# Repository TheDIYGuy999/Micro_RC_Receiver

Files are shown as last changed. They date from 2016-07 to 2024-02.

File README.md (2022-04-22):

# This is an ATMEL Mega328P / NRF24L01+ based 2.4GHz radio receiver
## Features:
- Compatible with this transmitter: https://github.com/TheDIYGuy999/RC_Transmitter
- Programmable with Arduino IDE
- 4 RC servo connectors
- SBUS output
- Outputs for Headlights, indicators, taillights with brake lights
- Additional switching output
- Support for self balancing robot or car with stability control (using an MPU-6050 sensor)
- Integrated TB6612FNG dual dc motor driver
- Serial header (with SBUS support)
- I2C header (for example for the supported MPU-6050)
- ICSP header for programming with Arduino IDE (use "TheDIYGuy999 328P" board definition and set brownout voltage to 1.8V)
- NRF24L01+ SMD module integrated
- very small size
- Up to 20 vehicle addresses selectable, allows to use the same remote controller for 10 vehicles
- Eagle & Gerber files are also provided, if you want to build your own receiver!

See: https://www.youtube.com/playlist?list=PLGO5EJJClJBCjIvu8frS7LrEU3H2Yz_so

New in V 1.3:
- Vehicle configuration is now stored in "vehicleConfig.h", so the main code always stays the same.
- Crude frequency hopping, if bad receiving quality is detected (needs to be improved).

New in V 1.4:
- 10 vehicle addresses instead of 5
- More vehicle configuration options
- The "BACK" button on the transmitter can now be used (if the menu screen is not displayed on the OLED) as a momentary button, for example for a horn on the vehicle. It is sent as "data.momentary1"
- SimpleTimer library replaced with my own code, which uses significantly less memory

New in V 1.5:
- Added steering mixer for semi caterpillar and caterpillar vehicles such as tanks, diggers etc.
- Channel 3 is throttle, channel 1 is steering
- More vehicle configuration options in vehicleVonfig.h
- The left caterpillar is motor 2, the right is motor 1
- Steering servo 1 can be used in parallel (for semi caterpillar vehicles or vehicles with electronic differential)

New in V 1.6:
- Added indicator lights - wired to A4 (SDA) / A5 (SCL) ports
- enabled and disabled left / right by channel 4 left / right
- disabled by turning back the steering wheel (channel 1) - just like a real car
- hazard lights (all indicators flashing), if no connection to the transmitter

New in V 1.61:
- Battery cutoff bug fixed

New in V 1.7 (Support for board revision 1.3):
- **** TB6612FNG library update to V1.1 is required! ****
- motor driver pinout has changed in board V1.3. So we are now able to adjust the PWM frequency of motor2. This allows smooth motor operation without the typical PWM whining.
- vehicleConfig.h changed: "boardVersion" and "HP" variables added. They allow to stay compatible with older board versions. Just select the correct configuration.
- The new "HP" (High Power) board version has only one motor driver channel, because both TB6612FNG channels are wired in parallel. It's able to supply 2.4A (average) / 6.4A (peak) so we can use bigger motors. This is useful for models, which use a steering servo and don't need a second motor channel.'
- automatic radio re-initialisation after signal timeout

New in V 1.71
- Battery monitoring and cutoff triggering improved. Under load, 0.3V are now added to the battery voltage to compensate the voltage drop. This allows to set the cutoff voltage to 3.6V, even with bigger loads.
- Vehicle #7 added.

New in V 1.8
- New "engineSound" variable in "vehicleconfig.h". True means, that the servo 3 pulse signal can be switched on and off, using the  channel 2 joystick. This switches the engine sound on my "Rc Engine Sound" unit on and off.

New in V 1.9
- New vehicle specific configuration section in vehicleConfig.h. The configuration is now done entirely during compilation time.

New in V 2.0
- vehicle Config.h: New vehicleType 3 (forklift) added. Motor 2 is used as lifting motor in this case. A servo is required as steering motor.
- Beacon lights can be wired to servo channel 4. Select "beacons = true" in this case. The beacons are flashing during vehicle movement and are switching off, after the vehicle did not move for 10s.

New in V 2.1
- Sounds for a STAR WARS R2-D2 robot can now be generated on servo channel 3
- "toneOut" variable added to vehicleConfig.h. True means, that servo 3 channel is generating sounds instead of a servo signal.
- Do not enable "toneOut" and "engineSound" at the same time.
- Note: the Arduino tone() function is blocking. So don't play sounds while driving ;-)

New in V 2.2
- **** TB6612FNG library update to V1.2 is required! **** https://github.com/TheDIYGuy999/TB6612FNG
- **** The PID library is required! **** https://github.com/br3ttb/Arduino-PID-Library/
- Support for self balancing (inverted pendulum, segway) vehicles. See: https://www.youtube.com/watch?v=zse9-l2Yo3Y)
- A MPU-6050 accelerometer & gyro module is used for the balancing data communication via SDA & SCL
- Note, that the receiver will not work, if your vehicleType is 4 (balancing) and no MPU-6050 is connected!
- Do not enable "balancing" and "indicators" at the same time.

New in V 2.21
- Gyro drift calibration bug fixed
- Changed the balancing controller refresh rate to 125Hz to reduce jitter on a 8MHz MCU. Reason: one program loop takes 4 - 7ms, so we can't use a time base of 4ms (=250Hz).

New in V 2.3
- MRSC (Micro RC Stability Control) added. This functionality is similar to the Traxxas TSM or ESC. See: https://www.youtube.com/watch?v=IPve7QpdLBc&t=5s
- The steering servo angle is compensated in accordance with the speed, the requested steering angle and the measured yaw rate, which is coming from the MPU-6050
- Basically the mrsc() function was added. The required yaw rate is already calculated in the balancing.h, which is already existing for self balancing robots
- If you want to use this functionality, you have to set the vehicleType to 5 in the vehicleConfig.h. Please note, that the receiver will not work, if no MPU-6050 is connected and the vehicleType is set to 4 or 5!

New in V 2.31
 - MRSC gain factor now depending on the potentiometer 1 value on the transmitter
 - Allows to fine adjust the MRSC during driving, depending on the requirements of the street surface
 - Note, that you need to connect a potentiometer to the analog input A6 of your transmitter!
 
 New in V 2.32
 - Flickering headlights bug in vehicleType 5 fixed
 - The accelerometer vectors are not processed anymore in vehicleType 5. This is only required for the self balancing robot (vehicleType 4)
 
 New in V 2.4
 - The I2C bus is scanned for an MPU-6050 sensor during the setup() sequence. The vehicleType is automatically changed to 0 (car without MRSC), if no sensor is detected.
 - This means, that a car with vehicleType 5 (MRSC Stability Control) can now also be used without an MPU-6050 plugged in.
 - Note, that the self balancing mode (vehicleType 4) always requires an MPU-6050. Otherwise the receiver will not start.
 
 New in V 2.41
 - The "indicators" variable is now locked and can't be enabled, if the SDA and SCL pins are in use for the MPU-6050 sensor. This is the case in vehicleMode 4 and 5.
 
 New in V 2.5
 - The MRSC stability control is now also working for cars without a steering servo
 - Code was added to control a DC steering motor (as found in cheap RC cars) in accordance with the MPU-6050 yaw rate
 - This is for example very useful for Coke Can Cars. See: https://www.youtube.com/watch?v=jr5yYBal3vk
 
 New in V 2.6
 - The MRSC stability control can now be used with transmitters without gain adjustment potentiometer
 - The following optional parameters in the vehicleConfig.h allow to use a fixed gain: MRSC_FIXED, mrscGain
 - Allows to add an MPU-6050 gyro to every vehicle. So we always have a closed loop steering control, even without a proper servo with potentiometer feedback
 - On the "Non-High-Power" receiver model, 0.3V battery voltage are not added anymore during driving. This is not useful, if there is not much current draw.
 
 New in V 2.7
 - The MRSC stability control gain adjustment knob can now be linked to servo CH4, if "potentiometer1" is set to "true" in vehicleConfig.h
 - This is useful, if an external MRSC stability control unit for 3 pin servos is used. See: https://github.com/TheDIYGuy999/MRSC_Adapter_3Pin_Servo
 - Servo CH4 is wired to pin 5 in this case. This allows to adjust the MRSC gain on the transmitter, just as with the internal MRSC stability control
 
 New in V 2.8
 - Added support for differential thrust controlled airplanes
 - Tested with a Piper J3 CUB from Banggood
 
 New in V 2.9
 - Added TWO_SPEED_GEARBOX option for mechanical two speed gearboxes, shifted by a servo, connected to CH2, controlled by "Mode 1" button
 - Example see vehicle CONFIG_WPL_B-36
 - See video: https://www.youtube.com/watch?v=EaOJE_GU5pk&t=1s
 
 New in V 3.0
 - Added TRACTOR_TRAILER_UNLOCK option. Used to operate the tractor trailer unlocking servo
 - Press the "Back / Pulse" button to unlock your trailer
 - See vehicle "CONFIG_JJRC_Q60" for example
 - Parts for 3D printing: https://www.thingiverse.com/thing:3399449
 
 New in V 3.1
 - Added THRE_SPEED_GEARBOX option for mechanical three speed gearboxes, shifted by a servo, connected to CH2, controlled by a 3 position switch, connected to CH2 Joystick input of the transmitter. A 10k resistor is reqired between GND and the input pin as well as between the input pin and VCC
 - Three individual servo positions can be programmed: lim2L, lim2C, lim2R
 - Example see vehicle CONFIG_HG_P407
 
 New in V 3.2
 - Added the "TXO_toggle1" variable: allows to toggle the TXO pin, using the "Back / Impulse" button on the transmitter
 - Useful for example for additional lights
 - Don't activate it in combination with "TXO_momentary1". Serial is not usable, if one of these booleans is set to true
 
 New in V 3.3
 - Added experimental support for serial communication with my "Arduino RC engine sound generator for ESP32": https://github.com/TheDIYGuy999/Rc_Engine_Sound_ESP32
 - Uncomment "#define SERIAL_COMMUNICATION" in Adjustments.h of the sound generator
 - Connect pin 36 "VP"of the sound generator  to pin "TXO" of the receiver (disable "TXO_momentary1", "TXO_toggle1" & "headLights" in vehicleConfig.h)
 
 New in V 3.31
 - "headlLights" must be inactive as well in order to use serial communication!
 
 New in V 3.32
 - "data.pot1" properly initialized (cauesd an issue on the ESP32 engine sound generator)
 
 New in V 3.4
 - SBUS support added (variable "SBUS_SERIAL" in vehicleConfiguration.h
 - Channel order and comments see sendSbusCommands()
 - You need to install my SBUS library: https://github.com/TheDIYGuy999/SBUS
 - Connect your servos or what ever to pin "TXO"  (disable "TXO_momentary1", "TXO_toggle1" & "headLights" in vehicleConfig.h)
 
 New in V 3.5
 - mode1, mode2 and momentary1 properly initialised before SBUS is enabled
 
 New in V 3.6
 - "vehicleType" 1 or 2 (tracked or half tracked mode steering mixer) is now working as well, if two ESC are connected to servo pins 2 and 3. In the past, it was only usable with the internal TB6612 dual DC motor driver.
 - Also works in combination with my ESP32 Engine Sound & Light Controller (SBUS & PWM Mode)
 
 New in V 3.7
 - Steering center position separately adjustable, using "#define STEERING_3_POINT_CAL" and "lim1C". This is useful for badly designed steering linkage geometries. Example see vehicle configuration "CONFIG_WPL_B_36_MODE1"
 
 New in V 3.8:
 - 20 vehicle addresses instead of 10
 - Less RAM usage
 - 2 speed transmission not shifting while standing still. This will protect the shifting servo.

New in V 3.81:
 - Libraries comments added
 
 New in V 3.9:
 - New "#define VEHICLE_TYPE_3_WITH_ESC" option for vehicle type 3. Allows to use both TB6612 FNG motor driver channels for other stuff
 - Used in "CONFIG_MECCANO_DUMPER"

## Usage

See pictures

Newest version v1.5:
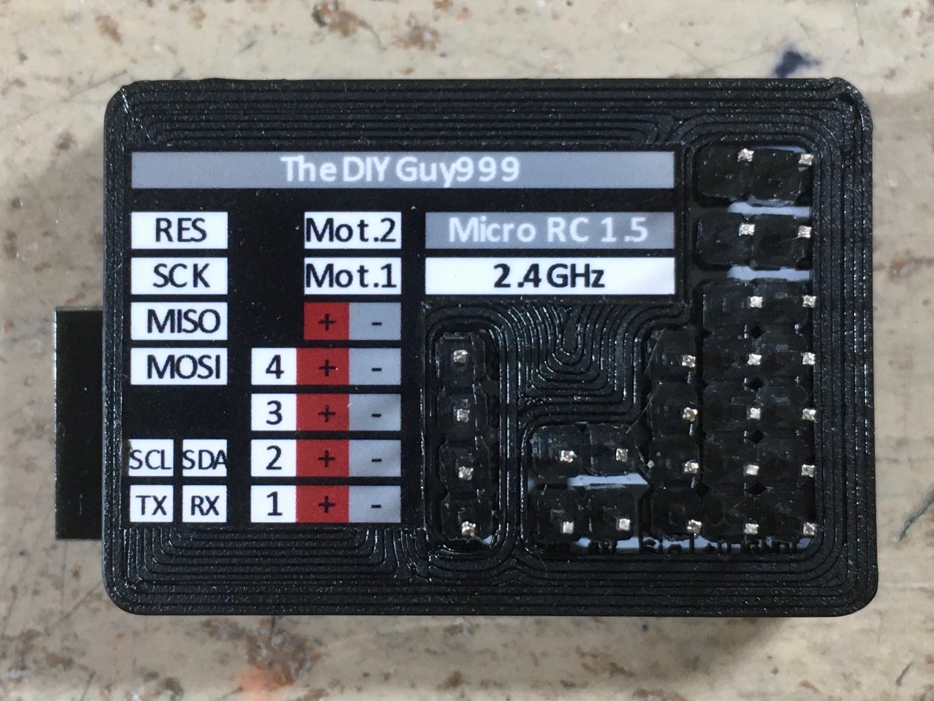
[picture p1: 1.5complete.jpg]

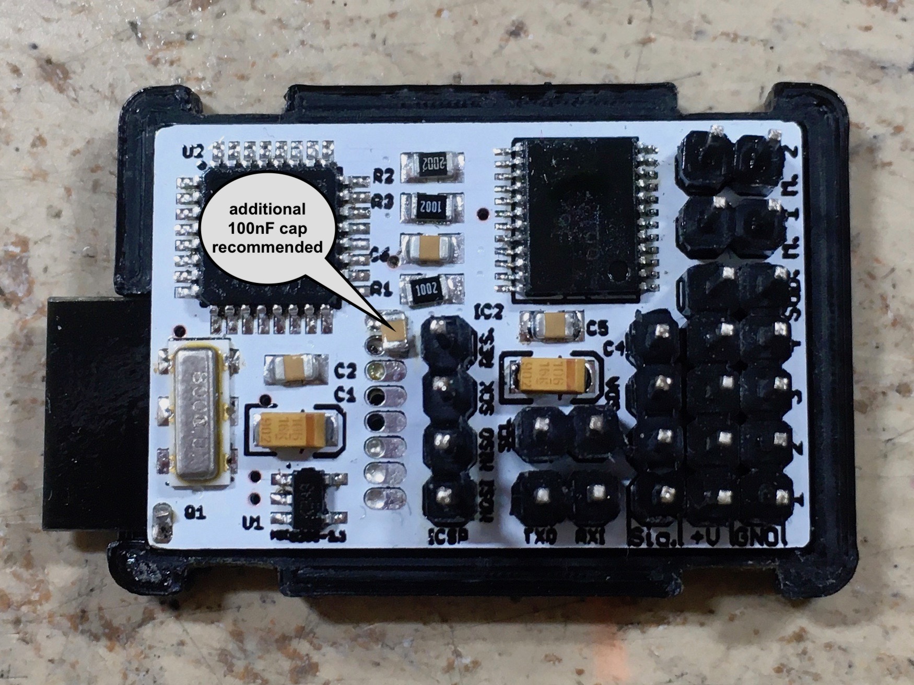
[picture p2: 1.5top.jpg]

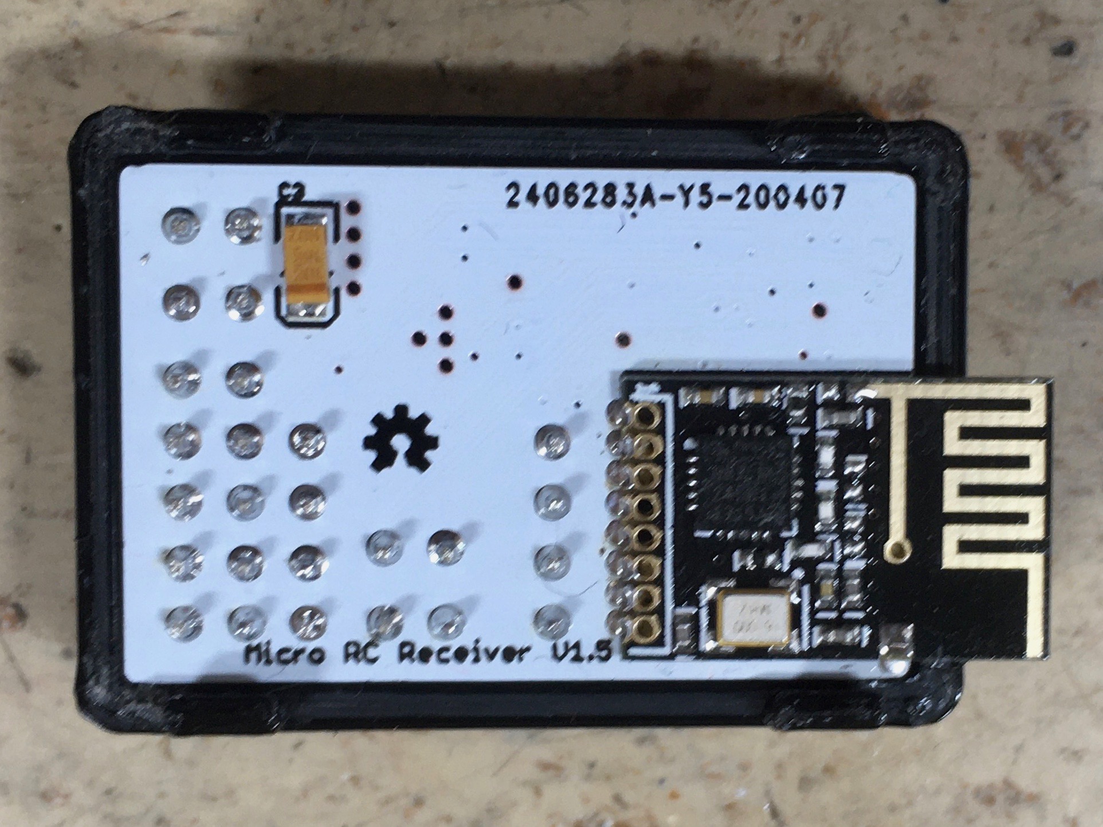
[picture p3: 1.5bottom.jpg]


First prototype:
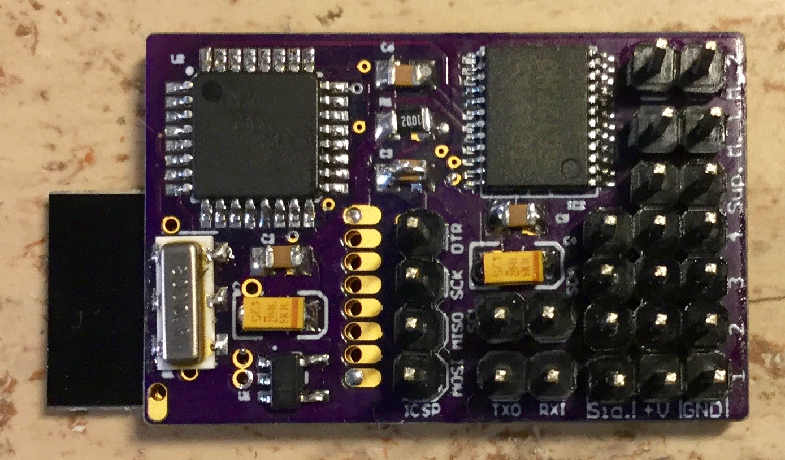
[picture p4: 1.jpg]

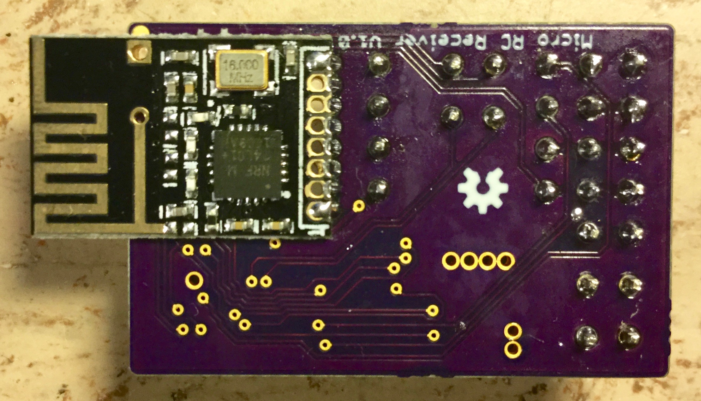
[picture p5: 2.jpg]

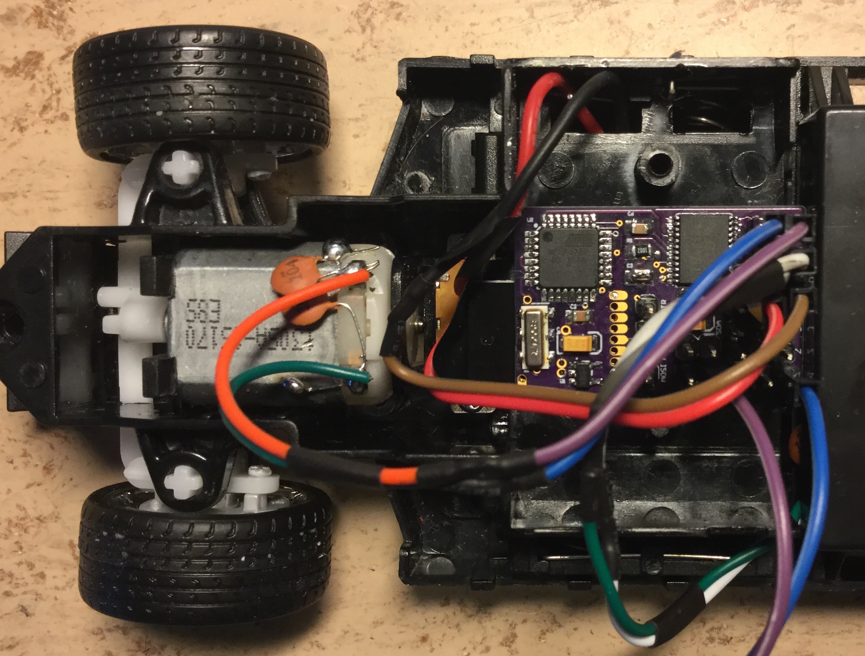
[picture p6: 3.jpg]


Receiver PCB

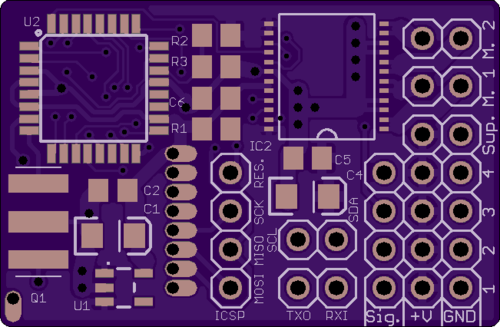
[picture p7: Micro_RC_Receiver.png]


MPU-6050 shield PCB

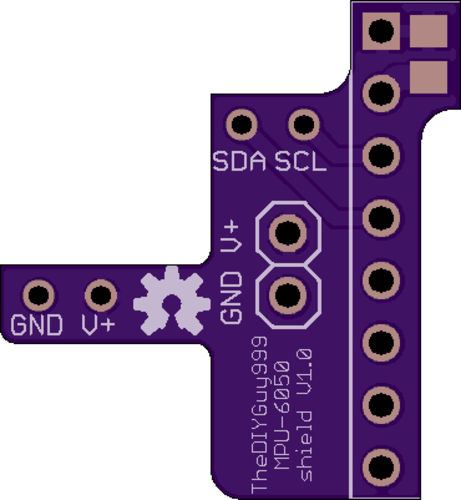
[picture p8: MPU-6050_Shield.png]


(c) 2016 - 2020 TheDIYGuy999

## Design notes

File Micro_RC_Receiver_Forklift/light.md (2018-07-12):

## light pins

|    light         |   pin  |
| ----------- ---- |   ---  |
|  tail light      | Servo2 |
|  head light      |  RXI   |
|  left indicator  |  SDA   |
|  right indicator |  SCL   |
|  beacon lights   | Servo4 |

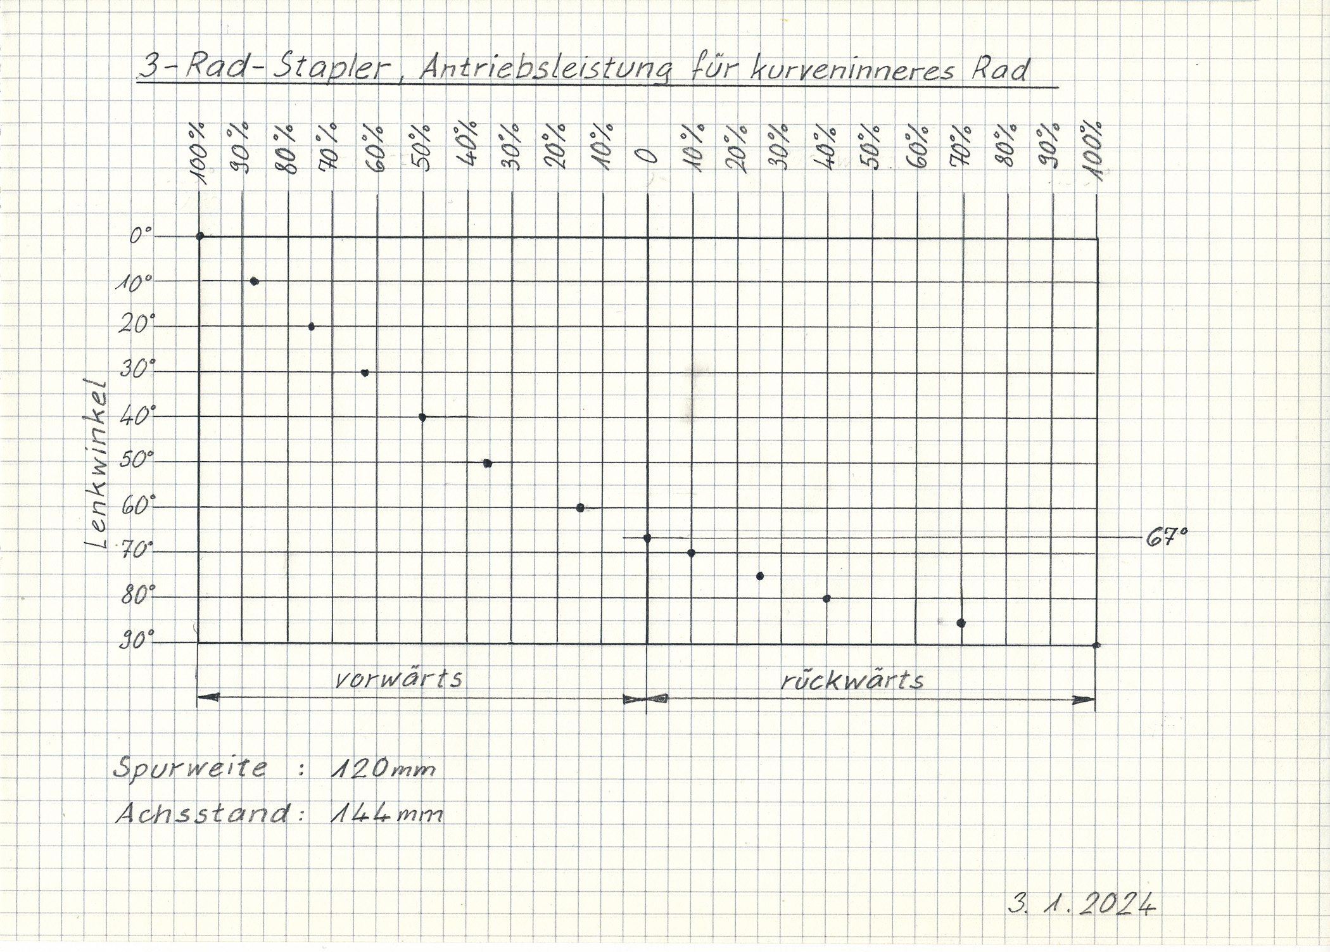
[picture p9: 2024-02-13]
Antriebaufteilung Stapler.jpg

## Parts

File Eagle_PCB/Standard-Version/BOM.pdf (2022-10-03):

## Micro RC Receiver Bill of Material

Qty. | Schematic | Package | Name | Value | Function | Manufacturor | Datasheet or Product Link
1 | U1 | SOT23-5 | MIC5205-3.3 | 3.3V | LDO 3.3V regulator | MICREL | http://ww1.microchip.com/downloads/en/DeviceDoc/mic5205.pdf
1 | U2 | TQFP32-08 | ATMEGA328P U-TH | | Microcontroller | MICROCHIP | http://www.atmel.com/images/Atmel-8271-8-bit-AVR-Microcontroller-ATmega48A-48PA-88A-88PA-168A-168PA-328-328P_datasheet_Complete.pdf
1 | IC1 | SMD PCB | NRF24L01+ | | Radio module (on a PCB) | NORDIC SEMI | https://www.sparkfun.com/datasheets/Components/SMD/nRF24L01Pluss_Preliminary_Product_Specification_v1_0.pdf
1 | IC2 | SSOP24 | TB6612FNG | | 2 Channel DC Motor Driver | TOSHIBA | https://www.sparkfun.com/datasheets/Robotics/TB6612FNG.pdf
1 | Q1 | SMT | CSTCC8M00G53-R0 | | 8MHz Resonator | MURATA | https://www.distrelec.ch/Web/Downloads/_t/ds/cstcc_g_eng_tds.pdf
3 | C1, C3, C4 | EIA3216 | T491A106K016AT | 16VDC, 10uF, Tantalum | Voltage smoothing | KEMET | https://www.distrelec.ch/Web/Downloads/_t/ds/KEM_T2005_T491_eng_tds.pdf
3 | C2, C5, C6 | 0805 | C0805C104K5RACTU | 50V, 100nF, Ceramic | Decoupling | KEMET | https://www.distrelec.ch/Web/Downloads/_t/ds/KEM_C1002_X7R_SMD_eng_tds.pdf
2 | R1, R3 | 0805 | CRCW080510K0FKEA | 10kOhm, +-1% | Reset Pullup, A7 Pulldown | Vishay | https://www.distrelec.ch/Web/Downloads/a_/en/flD-CRCW-e3_data_en.pdf
1 | R2 | 0805 | CRCW080520K0FKEA | 20kOhm, +-1% | A7 Pullup to VBAT | Vishay
10 | JP 1 - 10 | 0.1" | Pin Header | Male | Connectors | Generic

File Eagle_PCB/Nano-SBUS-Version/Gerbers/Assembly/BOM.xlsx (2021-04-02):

Comment | Designator | qty | Footprint | Additional Comment | 5sets Unite price | 5sets Total price | Note
ATmega328P-MU | U2 | 1 | MLF32-PAD | Arduino compatible | $3.675 | $18.375 | ATMEGA328P-MU
 | ~~IC1~~ |  | ~~NRF24L01_SMD_PAD~~ |  |  |  | DNP
 | ~~JP3, JP6~~ |  | ~~1X03_1.27~~ |  |  |  | DNP
 | ~~JP1~~ |  | ~~1X03_SMT~~ |  |  |  | DNP
 | ~~JP4~~ |  | ~~1X04_1.27~~ |  |  |  | DNP
 | ~~JP7~~ |  | ~~1X05_1.27~~ |  |  |  | DNP
 | ~~JP5~~ |  | ~~1X06_1.27~~ |  |  |  | DNP
100nF 50V | C2, C4 | 2 | C0603 |  | $0.052 | $0.525
10k | R1, R3 | 2 | R0603 |  | $0.052 | $0.525
10uF 16V Tantalum | C1 | 1 | EIA3216 |  | $0.210 | $1.050
20k | R2 | 1 | R0603 |  | $0.052 | $0.263
CSTNE8M00G550000R0 | Y2 | 1 | RESONATOR-SMD-3.2X1.3 | 8MhHz, Murata | $0.315 | $1.575
MIC5205-3.3 | U1 | 1 | SOT23-5 | 3.3V | $0.315 | $1.575 | MIC5205-3.3YM5-TR
 |  |  |  |  |  | $23.887 | Component price
 | Parts suppliers and tolerances are not important. Please ask back, if any of the SMD components can't be populated |  |  |  |  | $30.000 | assembly price
 |  |  |  |  |  | $15.000 | board price

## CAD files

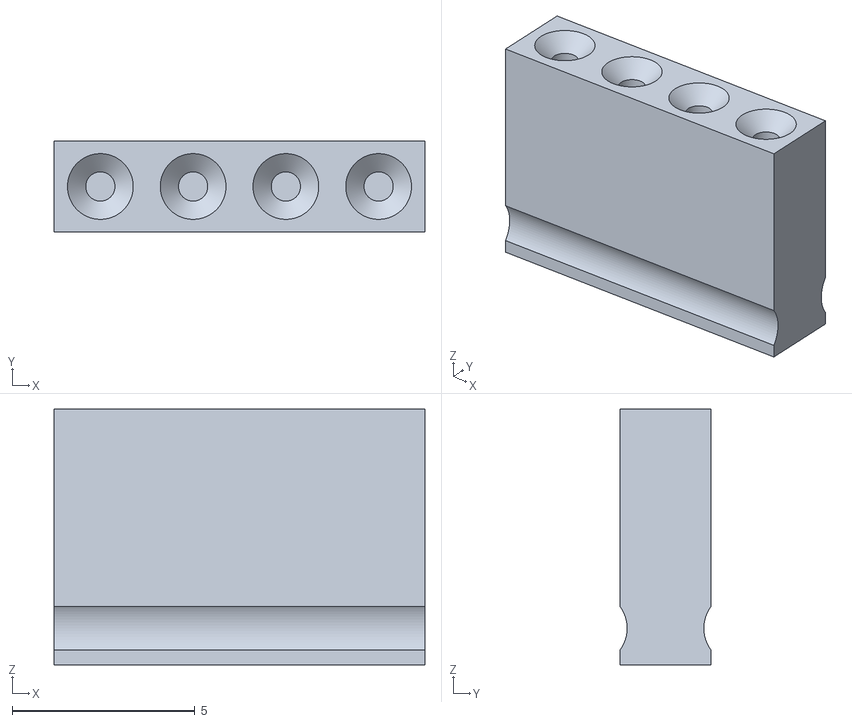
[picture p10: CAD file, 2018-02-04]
Housing/Pin Header Cover 4x.stl
10.2 x 2.50 x 7.00

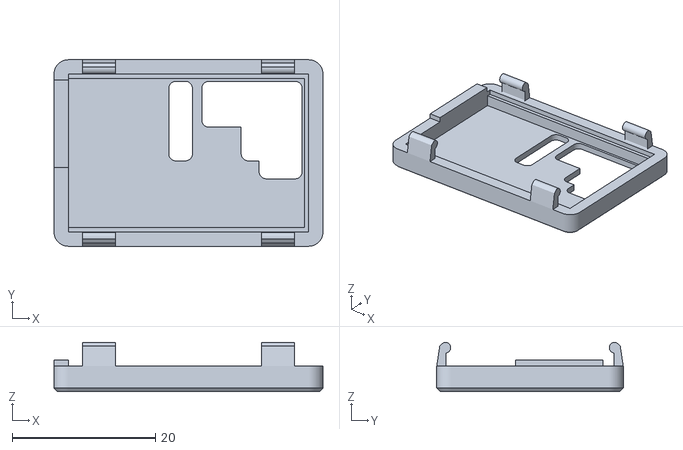
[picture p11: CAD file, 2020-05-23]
Housing/with clips/Receiver Top Clip No Motor.stl
37.5 x 26.0 x 6.90

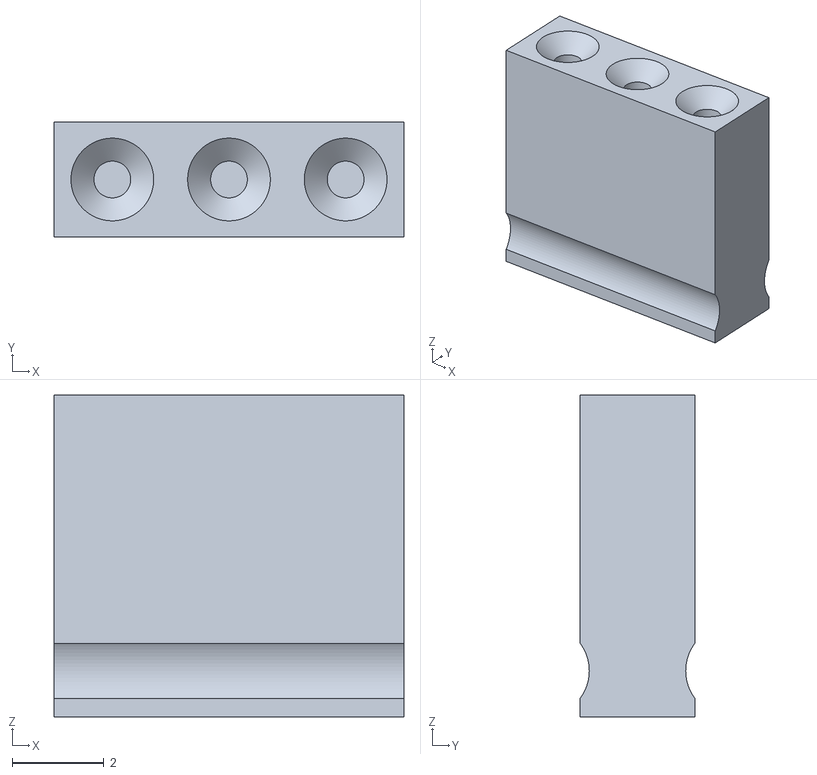
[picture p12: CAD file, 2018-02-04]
Housing/Pin Header Cover 3x.stl
7.62 x 2.50 x 7.00

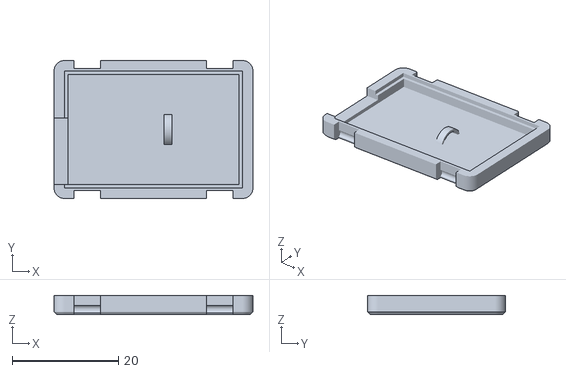
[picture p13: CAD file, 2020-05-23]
Housing/with clips/Receiver_Bottom_Clip.stl
37.5 x 26.0 x 3.60

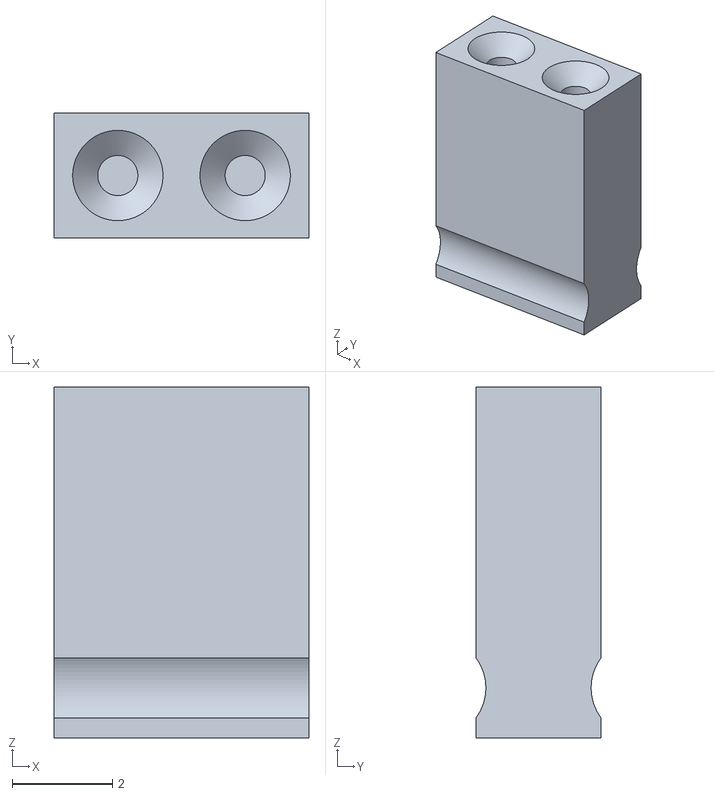
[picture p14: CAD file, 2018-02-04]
Housing/Pin Header Cover 2x.stl
5.08 x 2.50 x 7.00

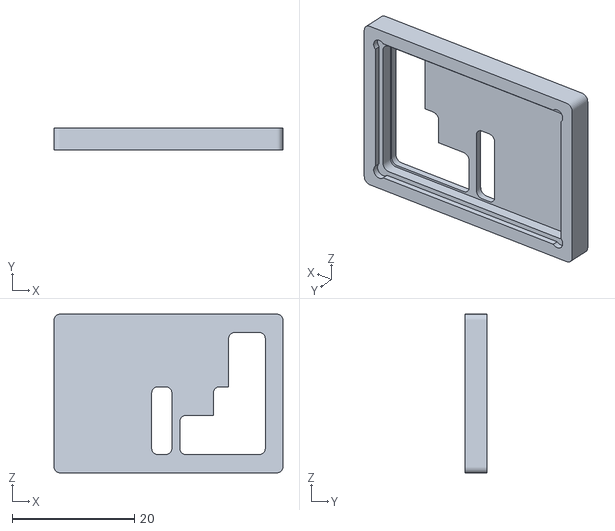
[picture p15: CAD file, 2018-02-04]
Housing/Top Housing Dual DC Motors.stl
37.5 x 3.60 x 26.0

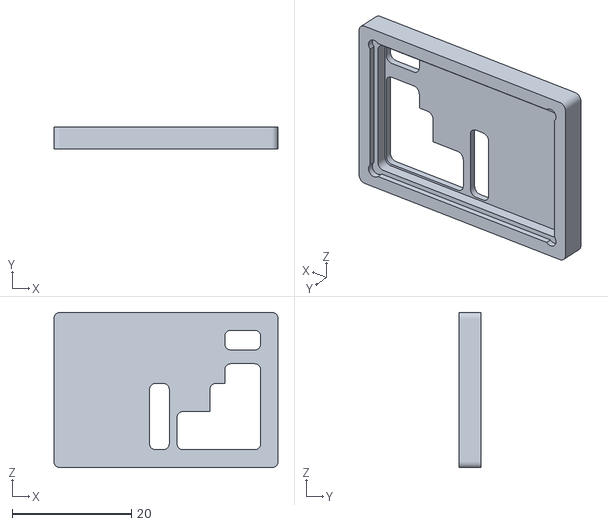
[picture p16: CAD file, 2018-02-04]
Housing/Top Housing High Power.stl
37.5 x 3.60 x 26.0

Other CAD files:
Housing/with clips/Receiver Top Clip Single Motor.stl
Housing/with clips/Receiver Top Clip Dual Motors.stl
Housing/Top Housing No DC Motor.stl
Housing/Bottom Housing.stl

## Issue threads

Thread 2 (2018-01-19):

Compatible Servos

milanico2309, 2018-01-19:
i want to put this in a wl-a959b and combine it with a new servo. what kind of servo do i need? analog/digital 3-wire/5-wire??? etc. Any recommendations, wich servo i should take?

TheDIYGuy999, 2018-01-30:
You can use any standard 3 pin servo

Closed 2018-02-11.

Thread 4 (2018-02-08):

BOM typo

ybunyak, 2018-02-08:
BOM file has an error: it says ATMEGA238P, but it should be ATMEGA328P, right?

TheDIYGuy999, 2018-02-11:
Fixed

Closed 2018-02-11.

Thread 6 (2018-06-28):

WHY you attach servo on ADC PIN A0 A1?

jindaxia, 2018-06-28:
I am a beginner on arduino and I cant understand the usage of servo attaching to adc pins
I only learned about servo attaching to the PWM pin
Can you explain
How it works?
Thank you very much

Closed 2018-06-28.

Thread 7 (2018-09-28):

UCSR0B was not declared in this scope

rari5, 2018-09-28:
I have followed everything about your video "Arduino 2.4GHz RC Receiver Scratch Build How To" but I have problem when uploading to pro micro 3.3v. There is some error and the message was 'UCSR0B' was not declared in this scope. What should I do? I am a beginner working with arduino. Would you mind telling me the full step to upload the code?

TheDIYGuy999, 2018-09-28:
For a step to step tutorial have a look at pages 18 - 20 of the transmitter manual: https://github.com/TheDIYGuy999/RC_Transmitter/blob/master/Manual_English.pdf

The board files for the Pro Micro can be found here: https://raw.githubusercontent.com/sparkfun/Arduino_Boards/master/IDE_Board_Manager/package_sparkfun_index.json
copy and paste this line in Preferences/Additional Boards Manager URLs:

Then install the Pro Micro boards in Tools/Boards Manager

Also don't mix up Pro Mini and Pro Micro boards. They have different processors.

rari5, 2018-09-29:
I have done with the  transmitter and It's worked, thank you. Pro micro board was installed correctly. But I couldn't upload the receiver like what I said before. As you said the code must burnt out before uploading to pro mini. I'm a little confused with that. Tell me if it's wrong, the code is uploaded to pro mico first and than burnt out with TheDIYguy999 328P board, the last step is uploading the code using "upload using programmer".

TheDIYGuy999, 2018-09-29:
What do you mean with "the code must burnt out before"? Yes, the boot loader must be burned before. Does the sketch compile (1st button from the left)? If not, post the error message.

Are the following libraries installed?
#include <statusLED.h> // https://github.com/TheDIYGuy999/statusLED
#include <TB6612FNG.h> // https://github.com/TheDIYGuy999/TB6612FNG ***NOTE*** V1.2 required!! <<<-----
#include <PWMFrequency.h> // https://github.com/TheDIYGuy999/PWMFrequency
#include <PID_v1.h> // https://github.com/br3ttb/Arduino-PID-Library/

All these .h files must be located in the same directory as your sketch:
#include "readVCC.h"
#include "vehicleConfig.h"
#include "steeringCurves.h"
#include "tone.h"
#include "balancing.h"
#include "helper.h"

rari5, 2018-09-29:
I have installed the libraries but for NR24.h installed from https://github.com/maniacbug/RF24 because I couldn't found at Boards Manager. Is it Ok?
#include <RF24.h> // Installed via Tools > Board > Boards Manager > Type RF24

I have tried tree boards for sketch compile :
1. Pro Mini 3.3v board was done compiling
2. TheDiyGuy999 board was done compiling
3. Pro Micro 3.3v board was error "exit status 1 / 'UCSR0B' was not declared in this scope" for detail message is below

note : For transmitter I used RC_Transmitter_STM32
  
Arduino: 1.8.7 (Windows 7), Board: "SparkFun Pro Micro, ATmega32U4 (3.3V, 8 MHz)"

C:\Program Files\Arduino\arduino-builder -dump-prefs -logger=machine -hardware C:\Program Files\Arduino\hardware -hardware C:\Users\Siti\AppData\Local\Arduino15\packages -tools C:\Program Files\Arduino\tools-builder -tools C:\Program Files\Arduino\hardware\tools\avr -tools C:\Users\Siti\AppData\Local\Arduino15\packages -built-in-libraries C:\Program Files\Arduino\libraries -libraries C:\Users\Siti\Documents\Arduino\libraries -fqbn=SparkFun:avr:promicro:cpu=8MHzatmega32U4 -ide-version=10807 -build-path C:\Users\Siti\AppData\Local\Temp\arduino_build_860709 -warnings=none -build-cache C:\Users\Siti\AppData\Local\Temp\arduino_cache_189953 -prefs=build.warn_data_percentage=75 -prefs=runtime.tools.avr-gcc.path=C:\Program Files\Arduino\hardware\tools\avr -prefs=runtime.tools.avr-gcc-5.4.0-atmel3.6.1-arduino2.path=C:\Program Files\Arduino\hardware\tools\avr -prefs=runtime.tools.arduinoOTA.path=C:\Program Files\Arduino\hardware\tools\avr -prefs=runtime.tools.arduinoOTA-1.2.1.path=C:\Program Files\Arduino\hardware\tools\avr -prefs=runtime.tools.avrdude.path=C:\Program Files\Arduino\hardware\tools\avr -prefs=runtime.tools.avrdude-6.3.0-arduino14.path=C:\Program Files\Arduino\hardware\tools\avr -verbose C:\Users\Siti\Documents\Arduino\Micro_RC_Receiver-master\Micro_RC_Receiver\Micro_RC_Receiver.ino
C:\Program Files\Arduino\arduino-builder -compile -logger=machine -hardware C:\Program Files\Arduino\hardware -hardware C:\Users\Siti\AppData\Local\Arduino15\packages -tools C:\Program Files\Arduino\tools-builder -tools C:\Program Files\Arduino\hardware\tools\avr -tools C:\Users\Siti\AppData\Local\Arduino15\packages -built-in-libraries C:\Program Files\Arduino\libraries -libraries C:\Users\Siti\Documents\Arduino\libraries -fqbn=SparkFun:avr:promicro:cpu=8MHzatmega32U4 -ide-version=10807 -build-path C:\Users\Siti\AppData\Local\Temp\arduino_build_860709 -warnings=none -build-cache C:\Users\Siti\AppData\Local\Temp\arduino_cache_189953 -prefs=build.warn_data_percentage=75 -prefs=runtime.tools.avr-gcc.path=C:\Program Files\Arduino\hardware\tools\avr -prefs=runtime.tools.avr-gcc-5.4.0-atmel3.6.1-arduino2.path=C:\Program Files\Arduino\hardware\tools\avr -prefs=runtime.tools.arduinoOTA.path=C:\Program Files\Arduino\hardware\tools\avr -prefs=runtime.tools.arduinoOTA-1.2.1.path=C:\Program Files\Arduino\hardware\tools\avr -prefs=runtime.tools.avrdude.path=C:\Program Files\Arduino\hardware\tools\avr -prefs=runtime.tools.avrdude-6.3.0-arduino14.path=C:\Program Files\Arduino\hardware\tools\avr -verbose C:\Users\Siti\Documents\Arduino\Micro_RC_Receiver-master\Micro_RC_Receiver\Micro_RC_Receiver.ino
Using board 'promicro' from platform in folder: C:\Users\Siti\AppData\Local\Arduino15\packages\SparkFun\hardware\avr\1.1.12
Using core 'arduino' from platform in folder: C:\Program Files\Arduino\hardware\arduino\avr
Build options changed, rebuilding all
Detecting libraries used...
"C:\\Program Files\\Arduino\\hardware\\tools\\avr/bin/avr-g++" -c -g -Os -w -std=gnu++11 -fpermissive -fno-exceptions -ffunction-sections -fdata-sections -fno-threadsafe-statics -flto -w -x c++ -E -CC -mmcu=atmega32u4 -DF_CPU=8000000L -DARDUINO=10807 -DARDUINO_AVR_PROMICRO -DARDUINO_ARCH_AVR -DUSB_VID=0x1b4f -DUSB_PID=0x9204 "-DUSB_MANUFACTURER=\"Unknown\"" "-DUSB_PRODUCT=\"SparkFun Pro Micro\"" "-IC:\\Program Files\\Arduino\\hardware\\arduino\\avr\\cores\\arduino" "-IC:\\Users\\Siti\\AppData\\Local\\Arduino15\\packages\\SparkFun\\hardware\\avr\\1.1.12\\variants\\promicro" "C:\\Users\\Siti\\AppData\\Local\\Temp\\arduino_build_860709\\sketch\\Micro_RC_Receiver.ino.cpp" -o nul
"C:\\Program Files\\Arduino\\hardware\\tools\\avr/bin/avr-g++" -c -g -Os -w -std=gnu++11 -fpermissive -fno-exceptions -ffunction-sections -fdata-sections -fno-threadsafe-statics -flto -w -x c++ -E -CC -mmcu=atmega32u4 -DF_CPU=8000000L -DARDUINO=10807 -DARDUINO_AVR_PROMICRO -DARDUINO_ARCH_AVR -DUSB_VID=0x1b4f -DUSB_PID=0x9204 "-DUSB_MANUFACTURER=\"Unknown\"" "-DUSB_PRODUCT=\"SparkFun Pro Micro\"" "-IC:\\Program Files\\Arduino\\hardware\\arduino\\avr\\cores\\arduino" "-IC:\\Users\\Siti\\AppData\\Local\\Arduino15\\packages\\SparkFun\\hardware\\avr\\1.1.12\\variants\\promicro" "-IC:\\Program Files\\Arduino\\hardware\\arduino\\avr\\libraries\\Wire\\src" "C:\\Users\\Siti\\AppData\\Local\\Temp\\arduino_build_860709\\sketch\\Micro_RC_Receiver.ino.cpp" -o nul
"C:\\Program Files\\Arduino\\hardware\\tools\\avr/bin/avr-g++" -c -g -Os -w -std=gnu++11 -fpermissive -fno-exceptions -ffunction-sections -fdata-sections -fno-threadsafe-statics -flto -w -x c++ -E -CC -mmcu=atmega32u4 -DF_CPU=8000000L -DARDUINO=10807 -DARDUINO_AVR_PROMICRO -DARDUINO_ARCH_AVR -DUSB_VID=0x1b4f -DUSB_PID=0x9204 "-DUSB_MANUFACTURER=\"Unknown\"" "-DUSB_PRODUCT=\"SparkFun Pro Micro\"" "-IC:\\Program Files\\Arduino\\hardware\\arduino\\avr\\cores\\arduino" "-IC:\\Users\\Siti\\AppData\\Local\\Arduino15\\packages\\SparkFun\\hardware\\avr\\1.1.12\\variants\\promicro" "-IC:\\Program Files\\Arduino\\hardware\\arduino\\avr\\libraries\\Wire\\src" "-IC:\\Users\\Siti\\Documents\\Arduino\\libraries\\RF24-master" "C:\\Users\\Siti\\AppData\\Local\\Temp\\arduino_build_860709\\sketch\\Micro_RC_Receiver.ino.cpp" -o nul
"C:\\Program Files\\Arduino\\hardware\\tools\\avr/bin/avr-g++" -c -g -Os -w -std=gnu++11 -fpermissive -fno-exceptions -ffunction-sections -fdata-sections -fno-threadsafe-statics -flto -w -x c++ -E -CC -mmcu=atmega32u4 -DF_CPU=8000000L -DARDUINO=10807 -DARDUINO_AVR_PROMICRO -DARDUINO_ARCH_AVR -DUSB_VID=0x1b4f -DUSB_PID=0x9204 "-DUSB_MANUFACTURER=\"Unknown\"" "-DUSB_PRODUCT=\"SparkFun Pro Micro\"" "-IC:\\Program Files\\Arduino\\hardware\\arduino\\avr\\cores\\arduino" "-IC:\\Users\\Siti\\AppData\\Local\\Arduino15\\packages\\SparkFun\\hardware\\avr\\1.1.12\\variants\\promicro" "-IC:\\Program Files\\Arduino\\hardware\\arduino\\avr\\libraries\\Wire\\src" "-IC:\\Users\\Siti\\Documents\\Arduino\\libraries\\RF24-master" "-IC:\\Program Files\\Arduino\\hardware\\arduino\\avr\\libraries\\SPI\\src" "C:\\Users\\Siti\\AppData\\Local\\Temp\\arduino_build_860709\\sketch\\Micro_RC_Receiver.ino.cpp" -o nul
"C:\\Program Files\\Arduino\\hardware\\tools\\avr/bin/avr-g++" -c -g -Os -w -std=gnu++11 -fpermissive -fno-exceptions -ffunction-sections -fdata-sections -fno-threadsafe-statics -flto -w -x c++ -E -CC -mmcu=atmega32u4 -DF_CPU=8000000L -DARDUINO=10807 -DARDUINO_AVR_PROMICRO -DARDUINO_ARCH_AVR -DUSB_VID=0x1b4f -DUSB_PID=0x9204 "-DUSB_MANUFACTURER=\"Unknown\"" "-DUSB_PRODUCT=\"SparkFun Pro Micro\"" "-IC:\\Program Files\\Arduino\\hardware\\arduino\\avr\\cores\\arduino" "-IC:\\Users\\Siti\\AppData\\Local\\Arduino15\\packages\\SparkFun\\hardware\\avr\\1.1.12\\variants\\promicro" "-IC:\\Program Files\\Arduino\\hardware\\arduino\\avr\\libraries\\Wire\\src" "-IC:\\Users\\Siti\\Documents\\Arduino\\libraries\\RF24-master" "-IC:\\Program Files\\Arduino\\hardware\\arduino\\avr\\libraries\\SPI\\src" "-IC:\\Program Files\\Arduino\\libraries\\Servo\\src" "C:\\Users\\Siti\\AppData\\Local\\Temp\\arduino_build_860709\\sketch\\Micro_RC_Receiver.ino.cpp" -o nul
"C:\\Program Files\\Arduino\\hardware\\tools\\avr/bin/avr-g++" -c -g -Os -w -std=gnu++11 -fpermissive -fno-exceptions -ffunction-sections -fdata-sections -fno-threadsafe-statics -flto -w -x c++ -E -CC -mmcu=atmega32u4 -DF_CPU=8000000L -DARDUINO=10807 -DARDUINO_AVR_PROMICRO -DARDUINO_ARCH_AVR -DUSB_VID=0x1b4f -DUSB_PID=0x9204 "-DUSB_MANUFACTURER=\"Unknown\"" "-DUSB_PRODUCT=\"SparkFun Pro Micro\"" "-IC:\\Program Files\\Arduino\\hardware\\arduino\\avr\\cores\\arduino" "-IC:\\Users\\Siti\\AppData\\Local\\Arduino15\\packages\\SparkFun\\hardware\\avr\\1.1.12\\variants\\promicro" "-IC:\\Program Files\\Arduino\\hardware\\arduino\\avr\\libraries\\Wire\\src" "-IC:\\Users\\Siti\\Documents\\Arduino\\libraries\\RF24-master" "-IC:\\Program Files\\Arduino\\hardware\\arduino\\avr\\libraries\\SPI\\src" "-IC:\\Program Files\\Arduino\\libraries\\Servo\\src" "-IC:\\Users\\Siti\\Documents\\Arduino\\libraries\\statusLED-master" "C:\\Users\\Siti\\AppData\\Local\\Temp\\arduino_build_860709\\sketch\\Micro_RC_Receiver.ino.cpp" -o nul
"C:\\Program Files\\Arduino\\hardware\\tools\\avr/bin/avr-g++" -c -g -Os -w -std=gnu++11 -fpermissive -fno-exceptions -ffunction-sections -fdata-sections -fno-threadsafe-statics -flto -w -x c++ -E -CC -mmcu=atmega32u4 -DF_CPU=8000000L -DARDUINO=10807 -DARDUINO_AVR_PROMICRO -DARDUINO_ARCH_AVR -DUSB_VID=0x1b4f -DUSB_PID=0x9204 "-DUSB_MANUFACTURER=\"Unknown\"" "-DUSB_PRODUCT=\"SparkFun Pro Micro\"" "-IC:\\Program Files\\Arduino\\hardware\\arduino\\avr\\cores\\arduino" "-IC:\\Users\\Siti\\AppData\\Local\\Arduino15\\packages\\SparkFun\\hardware\\avr\\1.1.12\\variants\\promicro" "-IC:\\Program Files\\Arduino\\hardware\\arduino\\avr\\libraries\\Wire\\src" "-IC:\\Users\\Siti\\Documents\\Arduino\\libraries\\RF24-master" "-IC:\\Program Files\\Arduino\\hardware\\arduino\\avr\\libraries\\SPI\\src" "-IC:\\Program Files\\Arduino\\libraries\\Servo\\src" "-IC:\\Users\\Siti\\Documents\\Arduino\\libraries\\statusLED-master" "-IC:\\Users\\Siti\\Documents\\Arduino\\libraries\\TB6612FNG-master" "C:\\Users\\Siti\\AppData\\Local\\Temp\\arduino_build_860709\\sketch\\Micro_RC_Receiver.ino.cpp" -o nul
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

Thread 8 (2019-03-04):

Winch motor

yudimoss, 2019-03-04:
Can I use rc winch with your receiver?

TheDIYGuy999, 2019-09-24:
Why not? connect it to one channel of the TB6612-FNG or use a separate small ESC

Closed 2019-09-24.

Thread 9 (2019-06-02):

B36

Ahmedabdulamir, 2019-06-02:
Hello again,

I see that you are using this receiver for the B36 WPL, I was wondering if you used the integrated receiver or just used an external ESC?. Im planning to use a Mini pro and a regular ESC as a receiver, but I feel hard to understand the change in the wiring diagram you posted. for the regular ESC you only supply PWD input. shall I connect only D3 to ESC?.

Thanks

TheDIYGuy999, 2019-11-10:
Just connect your ESC to the 3 pin servo connector CH3. In case you of a Pro Mini, connect it to Pin A2. Of course you have to connect GND and RAW as well

Closed 2019-11-10.

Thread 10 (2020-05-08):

Micro receiver question

stanekTM, 2020-05-08:
I want to thank you in advance for this amazing project.
This is exactly what I am looking for for my racing micro cars.
I will replace the original PCBs with new ones so that I can use the pistol transmitter from the OpenAVRc project.
Did I understand that the protocol is not compatible with any of the Multiprotokol projects ?
So I'll have to transfer the protocol.
Is there a project version NRF24L .. with its own RFU + MCU with motor driver control and servo channel output without additional processor ?
Thanks in advance for the inspiration.
George

TheDIYGuy999, 2020-07-08:
Thank you. Yes, the protocol is not compatible. Think it's not possible to control motor driver or servos without an additional MCU. Let me know, if you are able to transfer the protocol.

Closed 2020-07-08.

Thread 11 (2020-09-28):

Gerbers for receiver corrupt

debonthj, 2020-09-28:
Hi, I'd like to order some receiver PCB's but the gerber files seem to be corrupt? Tried on 2 computers. Thank you. https://github.com/TheDIYGuy999/Micro_RC_Receiver/blob/master/Eagle_PCB/Gerbers_V1.5.zip

TheDIYGuy999, 2020-09-28:
The Gerbes file is OK, i just tried on jlcpcb. you have to upload the entire zip, not just the files inside

Closed 2020-09-28.

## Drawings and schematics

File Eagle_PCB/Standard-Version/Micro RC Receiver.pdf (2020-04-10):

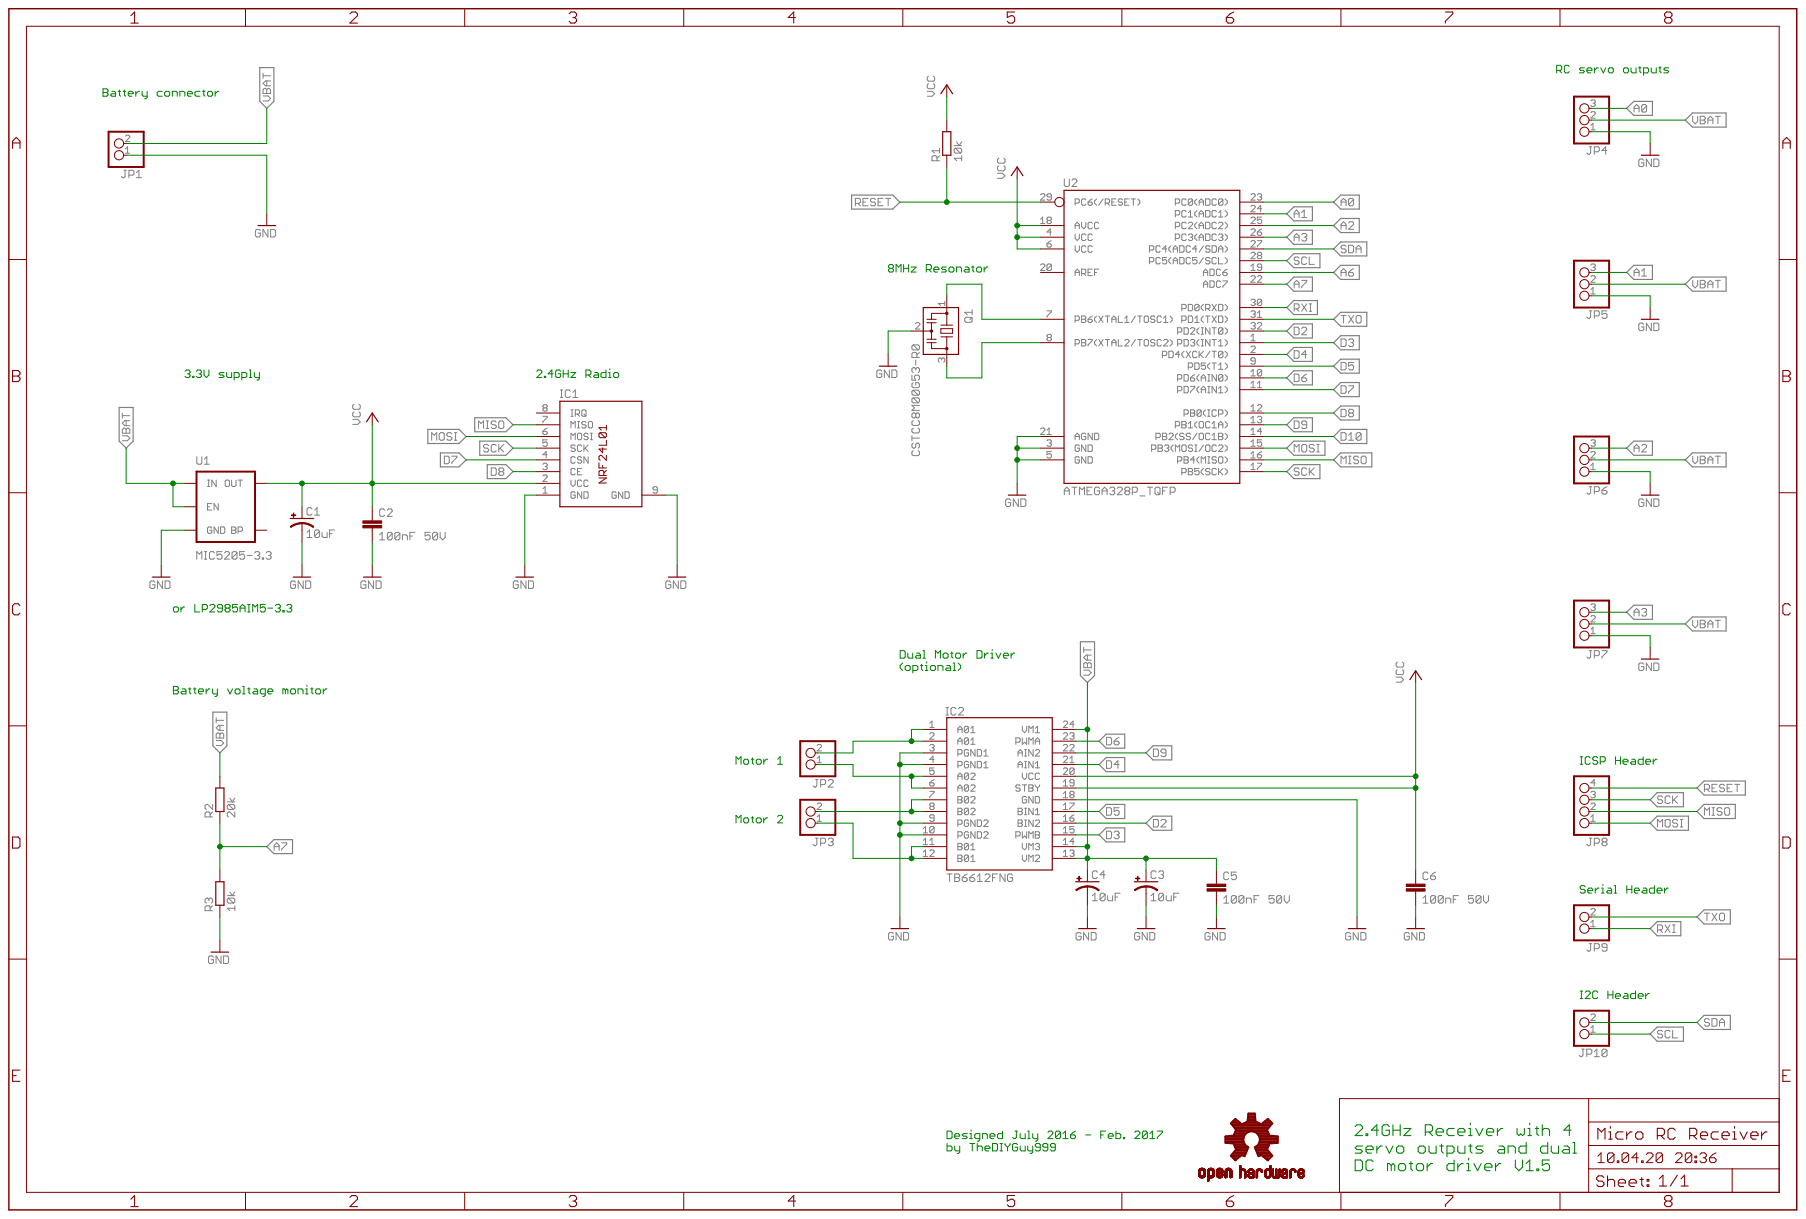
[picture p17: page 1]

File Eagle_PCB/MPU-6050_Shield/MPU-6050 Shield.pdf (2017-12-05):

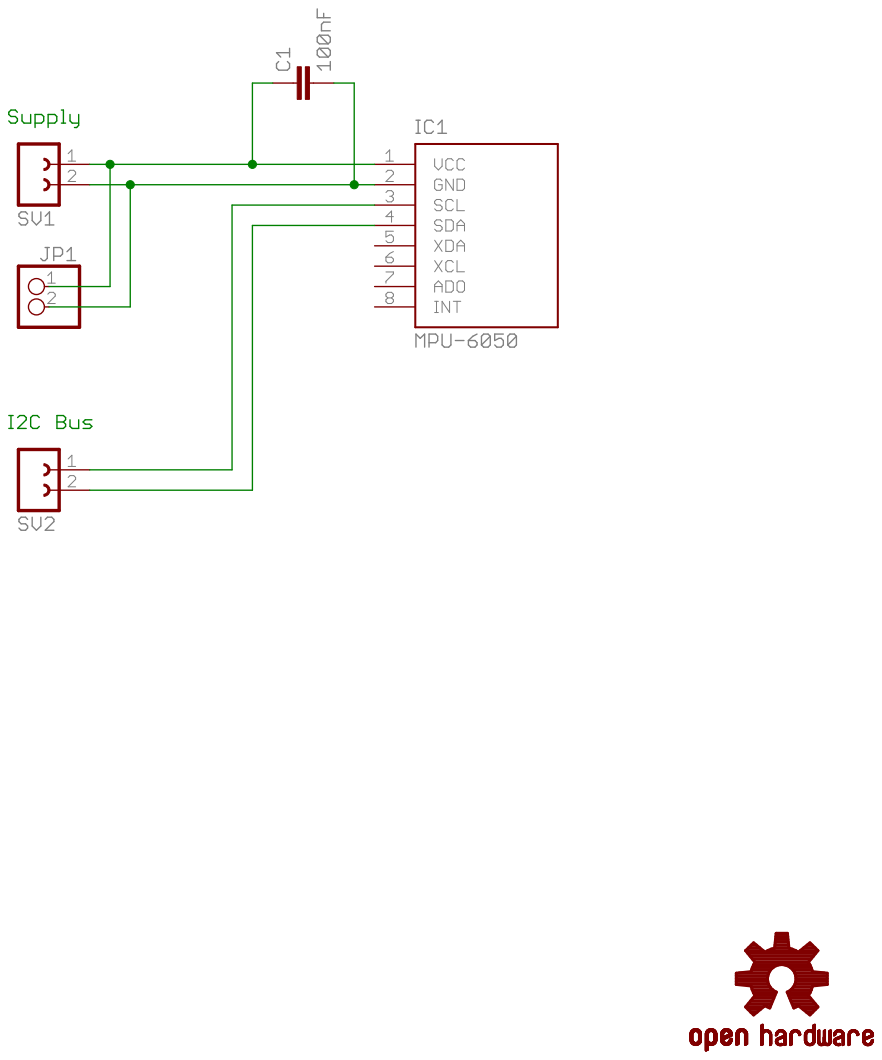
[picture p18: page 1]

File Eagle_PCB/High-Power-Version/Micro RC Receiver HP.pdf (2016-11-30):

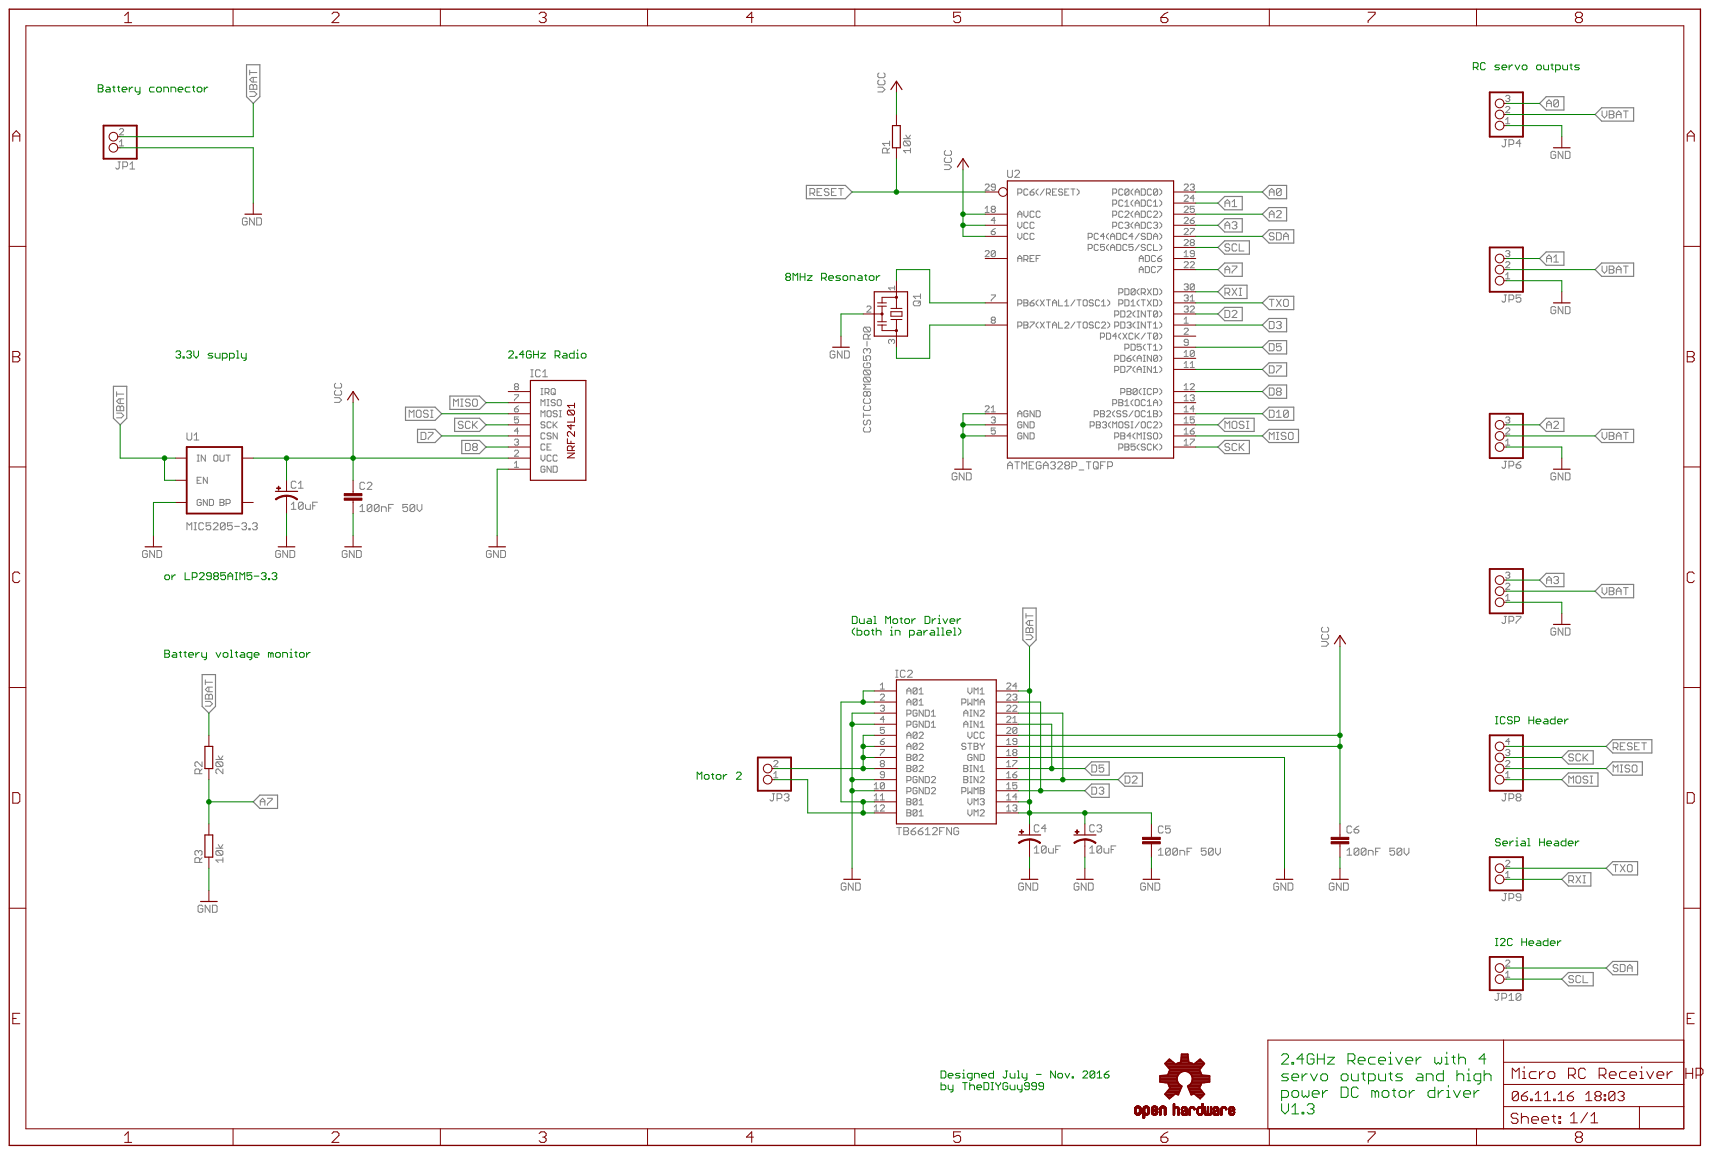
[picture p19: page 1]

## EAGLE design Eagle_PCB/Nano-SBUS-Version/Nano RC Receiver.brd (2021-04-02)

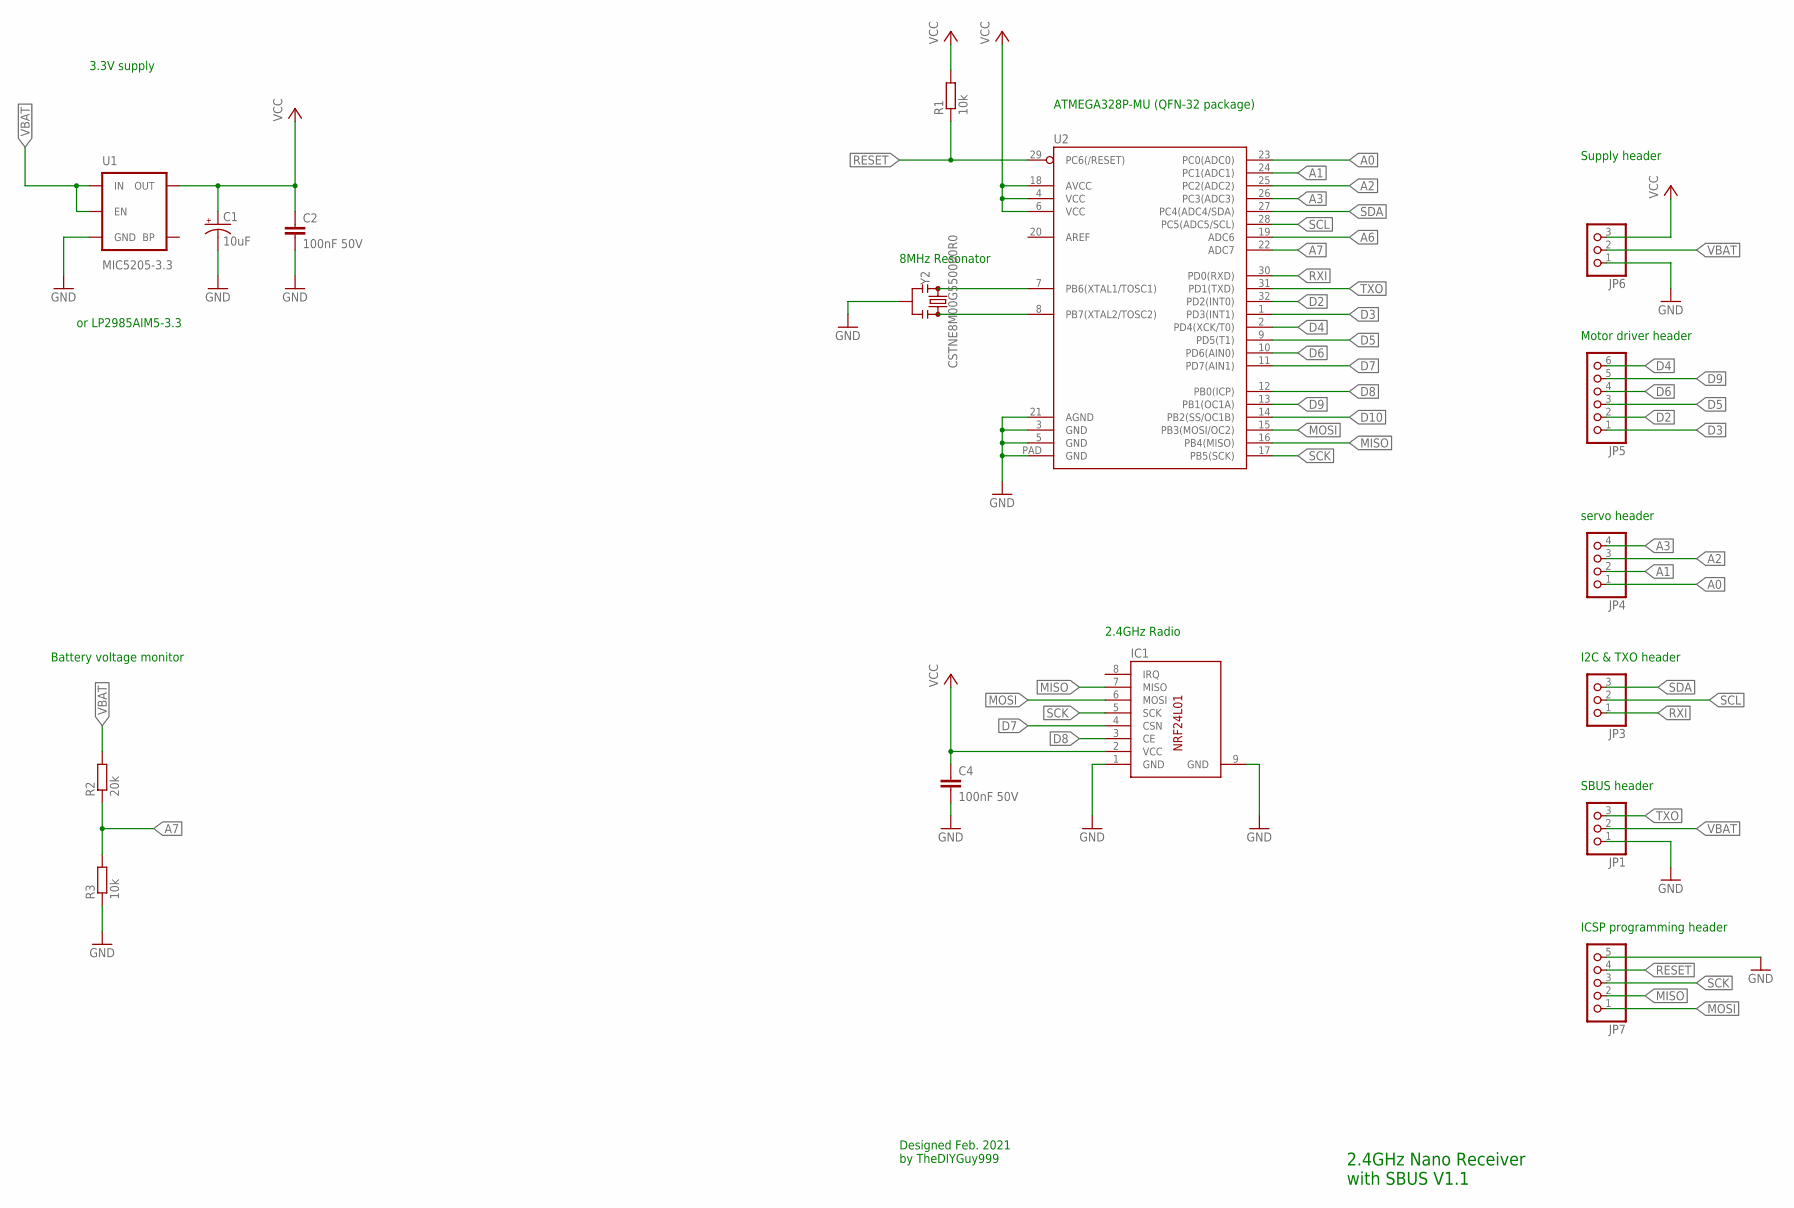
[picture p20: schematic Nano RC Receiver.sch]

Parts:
C1: 10uF; EIA3216
C2, C4: 100nF 50V; C0603
IC1: NRF24L01SMD_PAD; NRF24L01_SMD_PAD
JP1: PINHD-1X3SMT; 1X03_SMT
JP3, JP6: PINHD-1X31.27; 1X03_1.27
JP4: PINHD-1X41.27; 1X04_1.27
JP5: PINHD-1X61.27; 1X06_1.27
JP7: PINHD-1X51.27; 1X05_1.27
R1, R3: 10k; R0603
R2: 20k; R0603
U1: MIC5205-3.3; SOT23-5
U2: ATMEGA328P_MLFMLF32; MLF32-PAD
Y2: CSTNE8M00G550000R0; RESONATOR-SMD-3.2X1.3

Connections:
A0: JP4.1, U2.23 (PC0(ADC0))
A1: JP4.2, U2.24 (PC1(ADC1))
A2: JP4.3, U2.25 (PC2(ADC2))
A3: JP4.4, U2.26 (PC3(ADC3))
A6: U2.19 (ADC6)
A7: R2.1, R3.2, U2.22 (ADC7)
D2: JP5.2, U2.32 (PD2(INT0))
D3: JP5.1, U2.1 (PD3(INT1))
D4: JP5.6, U2.2 (PD4(XCK/T0))
D5: JP5.3, U2.9 (PD5(T1))
D6: JP5.4, U2.10 (PD6(AIN0))
D7: IC1.4 (CSN), U2.11 (PD7(AIN1))
D8: IC1.3 (CE), U2.12 (PB0(ICP))
D9: JP5.5, U2.13 (PB1(OC1A))
D10: U2.14 (PB2(SS/OC1B))
GND: C1.C (-), C2.2, C4.2, IC1.1 (GND), IC1.9 (GND), JP1.1, JP6.1, JP7.5, R3.1, U1.2 (GND), U2.3 (GND), U2.5 (GND), U2.21 (AGND), U2.PAD (GND), Y2.2
MISO: IC1.7 (MISO), JP7.2, U2.16 (PB4(MISO))
MOSI: IC1.6 (MOSI), JP7.1, U2.15 (PB3(MOSI/OC2))
RESET: JP7.4, R1.1, U2.29 (PC6(/RESET))
RXI: JP3.1, U2.30 (PD0(RXD))
SCK: IC1.5 (SCK), JP7.3, U2.17 (PB5(SCK))
SCL: JP3.2, U2.28 (PC5(ADC5/SCL))
SDA: JP3.3, U2.27 (PC4(ADC4/SDA))
TOSC1: U2.7 (PB6(XTAL1/TOSC1)), Y2.1
TOSC2: U2.8 (PB7(XTAL2/TOSC2)), Y2.3
TXO: JP1.3, U2.31 (PD1(TXD))
VBAT: JP1.2, JP6.2, R2.2, U1.1 (IN), U1.3 (EN)
VCC: C1.A (+), C2.1, C4.1, IC1.2 (VCC), JP6.3, R1.2, U1.5 (OUT), U2.4 (VCC), U2.6 (VCC), U2.18 (AVCC)

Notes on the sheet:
3.3V supply
2.4GHz Radio
2.4GHz Nano Receiver with SBUS V1.1
Designed Feb. 2021 by TheDIYGuy999
8MHz Resonator
or LP2985AIM5-3.3
Battery voltage monitor
ICSP programming header
servo header
SBUS header
I2C & TXO header
Motor driver header
Supply header
ATMEGA328P-MU (QFN-32 package)

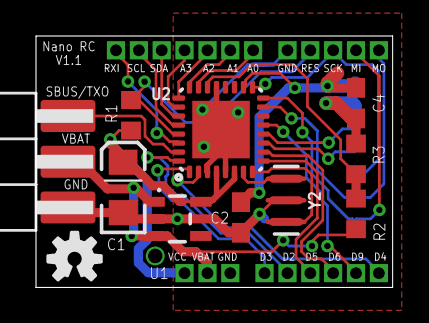
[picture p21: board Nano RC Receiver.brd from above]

Board: 2 copper layers, 19.8 x 14.0 mm, 17 parts (1 on the bottom side), 26 nets.

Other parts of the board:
LOGO2: OSHW-LOGOS; OSHW-LOGO-S

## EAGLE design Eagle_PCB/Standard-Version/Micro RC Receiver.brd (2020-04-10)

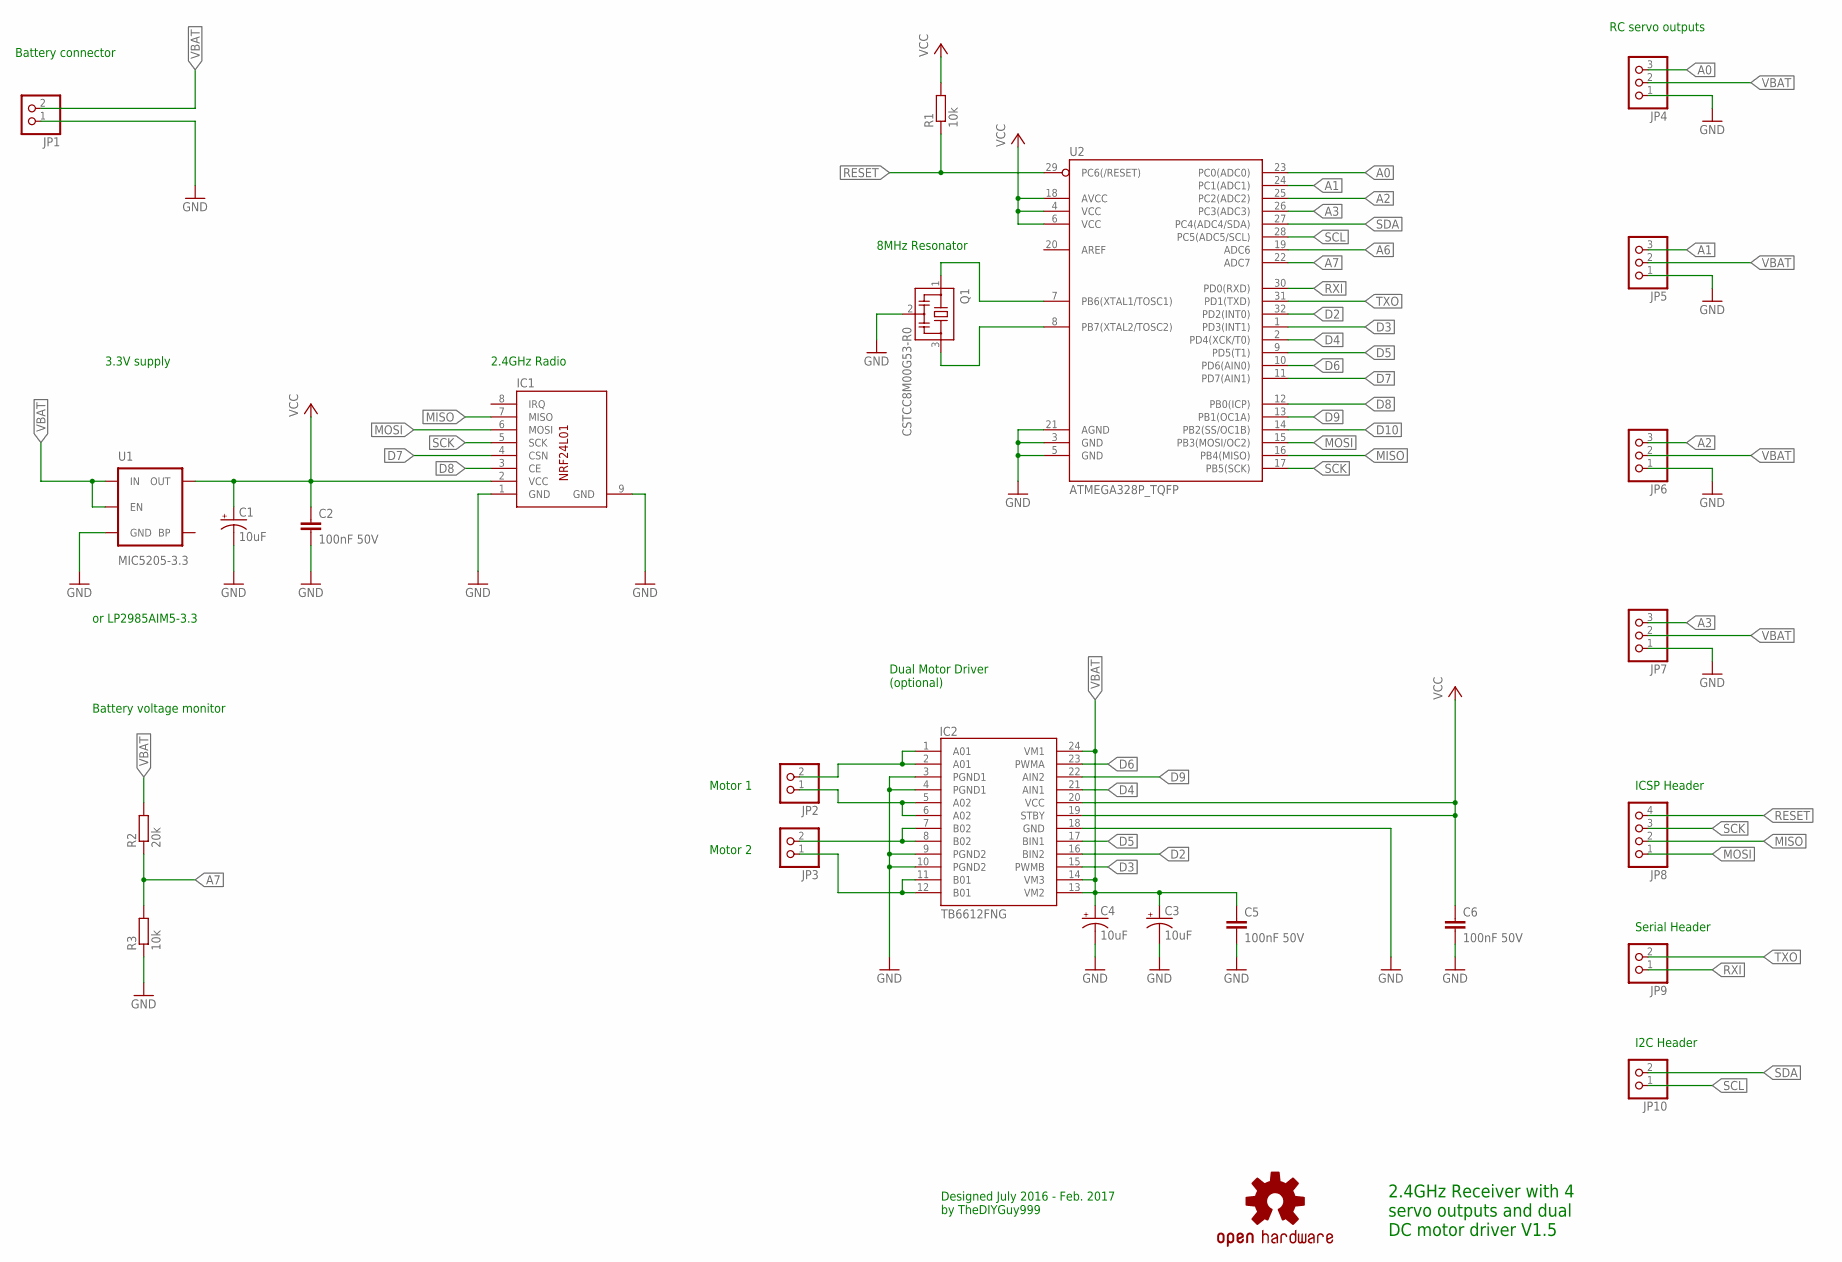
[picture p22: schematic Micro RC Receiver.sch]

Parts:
C1, C3, C4: 10uF; EIA3216
C2, C5, C6: 100nF 50V; C0805
IC1: NRF24L01SMD; NRF24L01_SMD
IC2: TB6612FNG; SSOP24
JP1, JP2, JP3, JP9, JP10: PINHD-1X2; 1X02
JP4, JP5, JP6, JP7: PINHD-1X3; 1X03
JP8: PINHD-1X4; 1X04
LOGO1: OSHW-LOGOS; OSHW-LOGO-S
Q1: CSTCC8M00G53-R0; CSTCC
R1, R3: 10k; R0805
R2: 20k; R0805
U1: MIC5205-3.3; SOT23-5
U2: ATMEGA328P_TQFP; TQFP32-08

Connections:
A0: JP4.3, U2.23 (PC0(ADC0))
A1: JP5.3, U2.24 (PC1(ADC1))
A2: JP6.3, U2.25 (PC2(ADC2))
A3: JP7.3, U2.26 (PC3(ADC3))
A6: U2.19 (ADC6)
A7: R2.1, R3.2, U2.22 (ADC7)
D2: IC2.16 (BIN2), U2.32 (PD2(INT0))
D3: IC2.15 (PWMB), U2.1 (PD3(INT1))
D4: IC2.21 (AIN1), U2.2 (PD4(XCK/T0))
D5: IC2.17 (BIN1), U2.9 (PD5(T1))
D6: IC2.23 (PWMA), U2.10 (PD6(AIN0))
D7: IC1.4 (CSN), U2.11 (PD7(AIN1))
D8: IC1.3 (CE), U2.12 (PB0(ICP))
D9: IC2.22 (AIN2), U2.13 (PB1(OC1A))
D10: U2.14 (PB2(SS/OC1B))
GND: C1.C (-), C2.2, C3.C (-), C4.C (-), C5.2, C6.2, IC1.1 (GND), IC1.9 (GND), IC2.3 (PGND1), IC2.4 (PGND1), IC2.9 (PGND2), IC2.10 (PGND2), IC2.18 (GND), JP1.1, JP4.1, JP5.1, JP6.1, JP7.1, Q1.2, R3.1, U1.2 (GND), U2.3 (GND), U2.5 (GND), U2.21 (AGND)
MISO: IC1.7 (MISO), JP8.2, U2.16 (PB4(MISO))
MOSI: IC1.6 (MOSI), JP8.1, U2.15 (PB3(MOSI/OC2))
unnamed: Q1.3, U2.8 (PB7(XTAL2/TOSC2))
unnamed: Q1.1, U2.7 (PB6(XTAL1/TOSC1))
unnamed: IC2.11 (B01), IC2.12 (B01), JP3.1
unnamed: IC2.7 (B02), IC2.8 (B02), JP3.2
unnamed: IC2.5 (A02), IC2.6 (A02), JP2.1
unnamed: IC2.1 (A01), IC2.2 (A01), JP2.2
RESET: JP8.4, R1.1, U2.29 (PC6(/RESET))
RXI: JP9.1, U2.30 (PD0(RXD))
SCK: IC1.5 (SCK), JP8.3, U2.17 (PB5(SCK))
SCL: JP10.1, U2.28 (PC5(ADC5/SCL))
SDA: JP10.2, U2.27 (PC4(ADC4/SDA))
TXO: JP9.2, U2.31 (PD1(TXD))
VBAT: C3.A (+), C4.A (+), C5.1, IC2.13 (VM2), IC2.14 (VM3), IC2.24 (VM1), JP1.2, JP4.2, JP5.2, JP6.2, JP7.2, R2.2, U1.1 (IN), U1.3 (EN)
VCC: C1.A (+), C2.1, C6.1, IC1.2 (VCC), IC2.19 (STBY), IC2.20 (VCC), R1.2, U1.5 (OUT), U2.4 (VCC), U2.6 (VCC), U2.18 (AVCC)

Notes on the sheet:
Motor 2
Motor 1
Dual Motor Driver (optional)
Battery connector
3.3V supply
2.4GHz Radio
RC servo outputs
2.4GHz Receiver with 4 servo outputs and dual DC motor driver V1.5
Designed July 2016 - Feb. 2017 by TheDIYGuy999
Serial Header
ICSP Header
I2C Header
8MHz Resonator
or LP2985AIM5-3.3
Battery voltage monitor

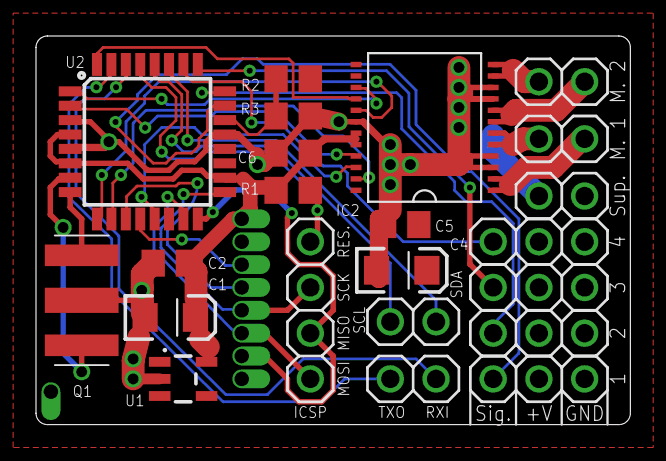
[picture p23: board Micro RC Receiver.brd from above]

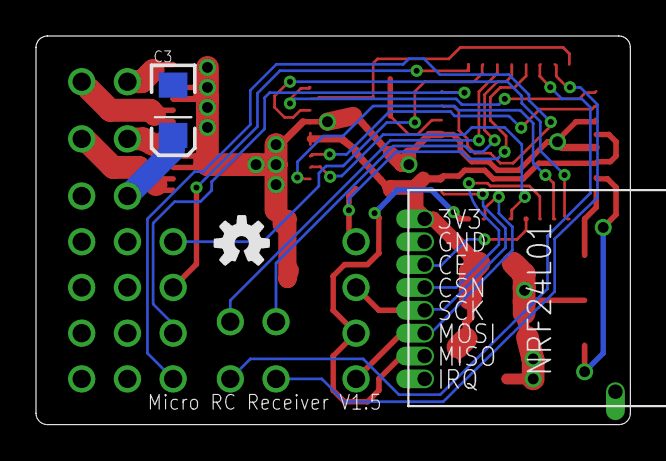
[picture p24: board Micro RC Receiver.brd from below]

Board: 2 copper layers, 33.0 x 21.6 mm, 25 parts (3 on the bottom side), 30 nets.

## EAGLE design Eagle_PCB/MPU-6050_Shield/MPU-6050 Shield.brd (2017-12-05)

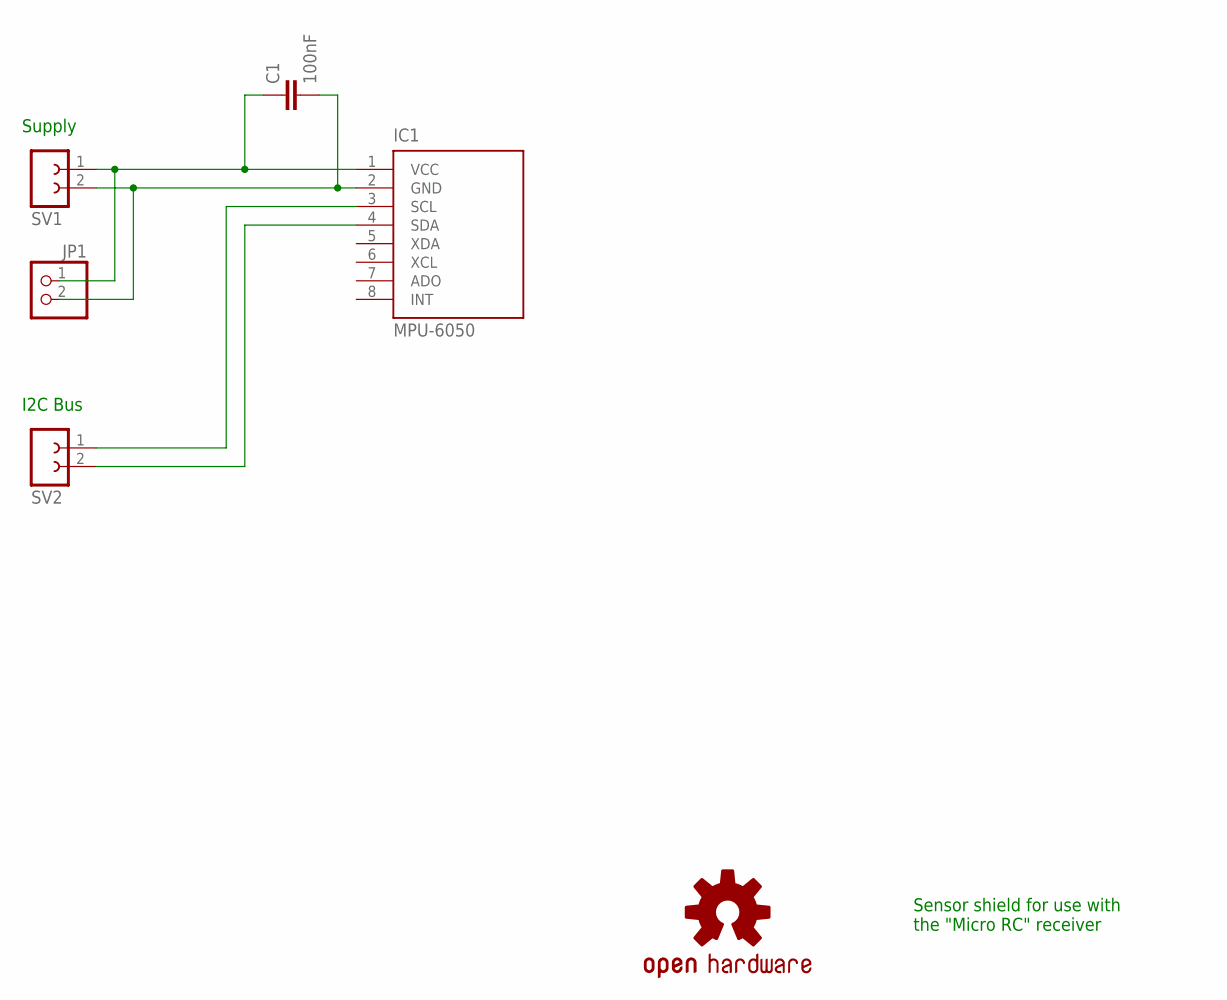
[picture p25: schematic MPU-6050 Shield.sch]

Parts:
C1: 100nF; C0805
IC1: MPU-6050; MPU-6050_GY521
JP1: PINHD-1X2; 1X02
LOGO1: OSHW-LOGOS; OSHW-LOGO-S
SV1, SV2: FE02-1

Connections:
GND: C1.2, IC1.2 (GND), JP1.2, SV1.2
unnamed: IC1.3 (SCL), SV2.1
unnamed: IC1.4 (SDA), SV2.2
VCC: C1.1, IC1.1 (VCC), JP1.1, SV1.1

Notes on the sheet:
Supply
I2C Bus
Sensor shield for use with the "Micro RC" receiver

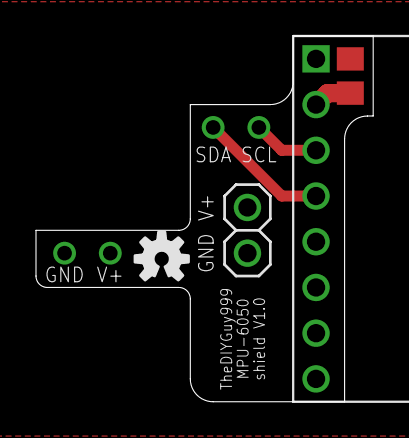
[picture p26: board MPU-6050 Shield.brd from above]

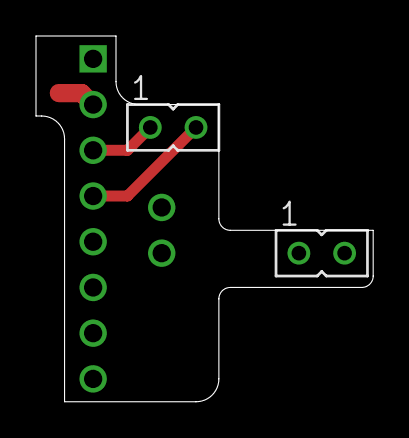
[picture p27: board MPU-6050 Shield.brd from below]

Board: 2 copper layers, 18.7 x 20.3 mm, 6 parts (2 on the bottom side), 4 nets.

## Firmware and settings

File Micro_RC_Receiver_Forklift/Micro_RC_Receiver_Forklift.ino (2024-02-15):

// 4 Channel "Micro RC" Receiver with 4 standard RC Servo Outputs
// ATMEL Mega 328P TQFP 32 soldered directly to the board, 8MHz external resonator,
// 2.4GHz NRF24L01 SMD radio module, TB6612FNG dual dc motor driver
// An MPU-6050 gyro / accelerometer can be used for MRSC stability control or self balancing robots
// SBUS output on pin TXO

// See: https://www.youtube.com/playlist?list=PLGO5EJJClJBCjIvu8frS7LrEU3H2Yz_so

// * * * * N O T E ! The vehicle specific configurations are stored in "vehicleConfig.h" * * * *

const float codeVersion = 3.9;  // Software revision (see https://github.com/TheDIYGuy999/Micro_RC_Receiver/blob/master/README.md)

//
// =======================================================================================================
// BUILD OPTIONS (comment out unneeded options)
// =======================================================================================================
//

//#define DEBUG // if not commented out, Serial.print() is active! For debugging only!!

//
// =======================================================================================================
// INCLUDE LIRBARIES
// =======================================================================================================
//

// Libraries
#include <RF24.h>  // Installed via Sketch > Include Library > Manage Libraries > Type "RF24" (use V1.3.3!)
#include <printf.h>
#include <Servo.h>
#include <TB6612FNG.h>     // https://github.com/TheDIYGuy999/TB6612FNG ***NOTE*** V1.2 required!! <<<-----
#include <PWMFrequency.h>  // https://github.com/TheDIYGuy999/PWMFrequency

// Tabs (header files in sketch directory)
#include "readVCC.h"
#include "vehicleConfig.h"
#include "steeringCurves.h"
#include "helper.h"
#include "pgmRead64.h"  // Read 64 bit blocks from PROGMEM

//
// =======================================================================================================
// PIN ASSIGNMENTS & GLOBAL VARIABLES
// =======================================================================================================
//

// Radio channels (126 channels are supported)
byte chPointer = 0;  // Channel 1 (the first entry of the array) is active by default
const byte NRFchannel[]{
  1, 2
};

// the ID number of the used "radio pipe" must match with the selected ID on the transmitter!
// 20 ID's are available @ the moment
const uint64_t pipeIn[] PROGMEM = {
  0xE9E8F0F0B1LL, 0xE9E8F0F0B2LL, 0xE9E8F0F0B3LL, 0xE9E8F0F0B4LL, 0xE9E8F0F0B5LL,
  0xE9E8F0F0B6LL, 0xE9E8F0F0B7LL, 0xE9E8F0F0B8LL, 0xE9E8F0F0B9LL, 0xE9E8F0F0B0LL,
  0xE9E8F0F0C1LL, 0xE9E8F0F0C2LL, 0xE9E8F0F0C3LL, 0xE9E8F0F0C4LL, 0xE9E8F0F0C5LL,
  0xE9E8F0F0C6LL, 0xE9E8F0F0C7LL, 0xE9E8F0F0C8LL, 0xE9E8F0F0C9LL, 0xE9E8F0F0C0LL
};
const int maxVehicleNumber = (sizeof(pipeIn) / (sizeof(uint64_t)));

// Hardware configuration: Set up nRF24L01 radio on hardware SPI bus & pins 8 (CE) & 7 (CSN)
RF24 radio(8, 7);

// The size of this struct should not exceed 32 bytes
struct RcData {
  byte axis1;                  // Tilt
  byte axis2;                  // Lift
  byte axis3;                  // Throttle
  byte axis4;                  // Steering
  boolean mode1 = false;       // Mode1 (toggle speed limitation)
  boolean mode2 = false;       // Mode2 (toggle acc. / dec. limitation)
  boolean momentary1 = false;  // Momentary push button
  byte pot1;                   // Potentiometer
};
RcData data;

// This struct defines data, which are embedded inside the ACK payload
struct ackPayload {
  float vcc;                 // vehicle vcc voltage
  float batteryVoltage;      // vehicle battery voltage
  boolean batteryOk = true;  // the vehicle battery voltage is OK!
  byte channel = 1;          // the channel number
};
ackPayload payload;

// Battery voltage detection pin
#define BATTERY_DETECT_PIN A7  // The 20k (to battery) & 10k (to GND) battery detection voltage divider is connected to pin A7

// Create Servo objects
Servo servo1;
Servo servo2;
Servo servo3;
Servo servo4;

// Special functions
#define DIGITAL_OUT_1 1  // 1 = TXO Pin

// Headlight off delay
unsigned long millisLightOff = 0;

// Indicators
bool left;
bool right;
bool hazard;

// Motors
bool isDriving;  // is the vehicle driving?

// Motor objects
TB6612FNG Motor1;
TB6612FNG Motor2;

// Serial commands to light and sound controller
boolean serialCommands;

// ESC variables for tracked and half tracked mode
int lEsc;
int rEsc;

// Channel buffer
byte CH3;
byte CH4;

//
// =======================================================================================================
// RADIO SETUP
// =======================================================================================================
//

void setupRadio() {
  radio.begin();
  radio.setChannel(NRFchannel[chPointer]);

  // Set Power Amplifier (PA) level to one of four levels: RF24_PA_MIN, RF24_PA_LOW, RF24_PA_HIGH and RF24_PA_MAX
  radio.setPALevel(RF24_PA_HIGH);  // HIGH

  radio.setDataRate(RF24_250KBPS);
  //radio.setAutoAck(pipeIn[vehicleNumber - 1], true); // Ensure autoACK is enabled
  radio.setAutoAck(pgm_read_64(&pipeIn, vehicleNumber - 1), true);  // Ensure autoACK is enabled
  radio.enableAckPayload();
  radio.enableDynamicPayloads();
  radio.setRetries(5, 5);  // 5x250us delay (blocking!!), max. 5 retries
  //radio.setCRCLength(RF24_CRC_8);          // Use 8-bit CRC for performance

#ifdef DEBUG
  radio.printDetails();
  delay(3000);
#endif

  //radio.openReadingPipe(1, pipeIn[vehicleNumber - 1]);
  radio.openReadingPipe(1, pgm_read_64(&pipeIn, vehicleNumber - 1));
  radio.startListening();
}

//
// =======================================================================================================
// MOTOR DRIVER SETUP
// =======================================================================================================
//

void setupMotors() {

  // TB6612FNG H-Bridge pins
  // ---- IMPORTANT ---- The pin assignment depends on your board revision and is switched here to match!
  const byte motor1_in1 = 4;
  const byte motor1_in2 = 9;
  const byte motor1_pwm = 6;

  byte motor2_in1;
  const byte motor2_in2 = 2;
  byte motor2_pwm;

  // Switchable pins:
  if (boardVersion >= 1.3) {  // Board version >= 1.3:
    motor2_in1 = 5;           // 5
    motor2_pwm = 3;           // 3
  } else {                    // Board Version < 1.3:
    motor2_in1 = 3;           // 3
    motor2_pwm = 5;           // 5
  }

  // SYNTAX: IN1, IN2, PWM, min. input value, max. input value, neutral position width
  // invert rotation direction true or false
  Motor1.begin(motor1_in1, motor1_in2, motor1_pwm, 0, 100, 4, false);  // Drive motor
  Motor2.begin(motor2_in1, motor2_in2, motor2_pwm, 0, 100, 4, false);  // Steering motor (Drive in "HP" version)

  // Motor PWM frequency prescalers (Requires the PWMFrequency.h library)
  // Differential steering vehicles: locked to 984Hz, to make sure, that both motors use 984Hz.
  if (vehicleType == 1 || vehicleType == 2 || vehicleType == 6) pwmPrescaler2 = 32;

  // ----------- IMPORTANT!! --------------
  // Motor 1 always runs @ 984Hz PWM frequency and can't be changed, because timers 0 an 1 are in use for other things!
  // Motor 2 (pin 3) can be changed to the following PWM frequencies: 32 = 984Hz, 8 = 3936Hz, 1 = 31488Hz
  setPWMPrescaler(3, pwmPrescaler2);  // pin 3 is hardcoded, because we can't change all others anyway
}

//
// =======================================================================================================
// MAIN ARDUINO SETUP (1x during startup)
// =======================================================================================================
//

void setup() {

  // All axes to neutral position
  data.axis1 = 50;
  data.axis2 = 50;
  data.axis3 = 50;
  data.axis4 = 50;
  data.pot1 = 50;
  data.mode1 = true;
  data.mode2 = true;
  data.momentary1 = false;

#ifdef DEBUG
  Serial.begin(115200);
  printf_begin();
  serialCommands = false;
  delay(3000);
#endif

  // Radio setup
  setupRadio();

  // Servo pins
  servo1.attach(A0);
  servo2.attach(A1);
  servo3.attach(A2);
  servo4.attach(A3);

  // Special functions
  if (TXO_momentary1 || TXO_toggle1) pinMode(DIGITAL_OUT_1, OUTPUT);

  // Motor driver setup
  setupMotors();
}

//
// =======================================================================================================
// READ RADIO DATA
// =======================================================================================================
//

void readRadio() {

  static unsigned long lastRecvTime = 0;
  byte pipeNo;

  if (radio.available(&pipeNo)) {
    radio.writeAckPayload(pipeNo, &payload, sizeof(struct ackPayload));  // prepare the ACK payload
    radio.read(&data, sizeof(struct RcData));                            // read the radia data and send out the ACK payload
    hazard = false;
    lastRecvTime = millis();
#ifdef DEBUG
    Serial.print(data.axis1);
    Serial.print("\t");
    Serial.print(data.axis2);
    Serial.print("\t");
    Serial.print(data.axis3);
    Serial.print("\t");
    Serial.print(data.axis4);
    Serial.println("\t");
#endif
  }

  // Switch channel
  if (millis() - lastRecvTime > 500) {
    chPointer++;
    if (chPointer >= sizeof((*NRFchannel) / sizeof(byte))) chPointer = 0;
    radio.setChannel(NRFchannel[chPointer]);
    payload.channel = NRFchannel[chPointer];
  }

  if (millis() - lastRecvTime > 1000) {  // set all analog values to their middle position, if no RC signal is received during 1s!
    data.axis1 = 50;                     // Aileron (Steering for car)
    data.axis2 = 50;                     // Elevator
    data.axis3 = 50;                     // Throttle
    data.axis4 = 50;                     // Rudder
    hazard = true;                       // Enable hazard lights
    payload.batteryOk = true;            // Clear low battery alert (allows to re-enable the vehicle, if you switch off the transmitter)
#ifdef DEBUG
    Serial.println("No Radio Available - Check Transmitter!");
#endif
  }

  if (millis() - lastRecvTime > 2000) {
    setupRadio();  // re-initialize radio
    lastRecvTime = millis();
  }
}

//
// =======================================================================================================
// EXPONENTIAL CURVES
// =======================================================================================================
//


void exponentialCurves() {
  static uint16_t CH3MicroSeconds;
  static uint16_t CH4MicroSeconds;

  if (data.mode2) {  // Use mode 2 button to switch between linear and exponential mode
    CH3MicroSeconds = map(data.axis3, 100, 0, 2000, 1000);
    CH3MicroSeconds = reMap(curveExponentialThrottle, CH3MicroSeconds);
    CH3 = map(CH3MicroSeconds, 2000, 1000, 100, 0);

    CH4MicroSeconds = map(data.axis4, 100, 0, 2000, 1000);
    CH4MicroSeconds = reMap(curveExponentialThrottle, CH4MicroSeconds);
    CH4 = map(CH4MicroSeconds, 2000, 1000, 100, 0);
  } else {
    CH3 = data.axis3;
    CH4 = data.axis4;
  }
}


//
// =======================================================================================================
// WRITE SERVO POSITIONS
// =======================================================================================================
//

void writeServos() {

  // lift ----------------------------
  servo2.write(map(data.axis2, 100, 0, lim2L, lim2R));

  // steering servo ----------------------------
  servo4.write(map(CH4, 100, 0, lim4L, lim4R));
}

//
// =======================================================================================================
// "STEERING" MOTOR DRIVING FUNCTION (throttle & steering overlay for caterpillar vehicles)
// =======================================================================================================
//

void driveMotorsSteering() {

  int pwm[2];

  // The steering overlay
  int steeringFactorLeft;
  int steeringFactorRight;
  int steeringFactorLeft2;
  int steeringFactorRight2;

  // The input signal range
  const int servoMin = 1;
  const int servoMax = 99;
  const int servoNeutralMin = 48;
  const int servoNeutralMax = 52;

  // Compute steering overlay:
  // The steering signal is channel 4 = CH4
  // 100% = wheel spins with 100% of the requested speed forward
  // -100% = wheel spins with 100% of the requested speed backward
  if (CH4 <= servoNeutralMin) {
    steeringFactorLeft = map(CH4, servoMin, servoNeutralMin, 0, 100);
    steeringFactorLeft = constrain(steeringFactorLeft, 0, 100);
  } else {
    steeringFactorLeft = 100;
  }

  if (CH4 >= servoNeutralMax) {
    steeringFactorRight = map(CH4, servoMax, servoNeutralMax, 0, 100);
    steeringFactorRight = constrain(steeringFactorRight, 0, 100);
  } else {
    steeringFactorRight = 100;
  }

  // Nonlinear steering overlay correction
  steeringFactorLeft2 = reMap(curveForklift, steeringFactorLeft);  // Caterpillar mode
  steeringFactorRight2 = reMap(curveForklift, steeringFactorRight);


  // Drive caterpillar motors
  // The throttle signal (for both caterpillars) is channel 3 = data.axis3
  // -100 to 100%
  pwm[0] = map(CH3, servoMin, servoMax, 100, -100) * steeringFactorRight2 / 100;
  pwm[1] = map(CH3, servoMin, servoMax, 100, -100) * steeringFactorLeft2 / 100;

  pwm[0] = map(pwm[0], 100, -100, 100, 0);  // convert -100 to 100% to 0-100 for motor control
  pwm[1] = map(pwm[1], 100, -100, 100, 0);

  lEsc = pwm[1];  // Output for dual ESC
  rEsc = pwm[0];

  // right motor ----------------------------
  servo1.write(map(rEsc, 0, 100, lim1L, lim1R));

  // left motor ----------------------------
  servo3.write(map(lEsc, 0, 100, lim3L, lim3R));
}

//
// =======================================================================================================
// DRIVE MOTORS FORKLIFT (lifting)
// =======================================================================================================
//

void driveMotors() {

  // SYNTAX: Input value, max PWM, ramptime in ms per 1 PWM increment
  // false = brake in neutral position inactive

  Motor2.drive(data.axis1, 0, steeringTorque, 0, false);  // The tower tilting motor
}

//
// =======================================================================================================
// WRITE DIGITAL OUTPUTS (SPECIAL FUNCTIONS)
// =======================================================================================================
//

void digitalOutputs() {

  static boolean wasPressed;

  if (TXO_momentary1) {  // only, if momentary function is enabled in vehicle configuration
    if (data.momentary1) {
      digitalWrite(DIGITAL_OUT_1, HIGH);
    } else digitalWrite(DIGITAL_OUT_1, LOW);
  }

  if (TXO_toggle1) {  // only, if toggle function is enabled in vehicle configuration

    if (data.momentary1 && !wasPressed) {
      digitalWrite(DIGITAL_OUT_1, !digitalRead(DIGITAL_OUT_1));
      wasPressed = true;
    }
    if (!data.momentary1) wasPressed = false;
  }
}

//
// =======================================================================================================
// CHECK RX BATTERY & VCC VOLTAGES
// =======================================================================================================
//

bool battSense;

void checkBattery() {

  if (boardVersion < 1.2) battSense = false;
  else battSense = true;

  // switch between load and no load contition
  if (millis() - millisLightOff >= 1000) {  // one s after the vehicle did stop
    isDriving = false;                      // no load
  } else {
    isDriving = true;  // under load
  }

  // Every 1000 ms, take measurements
  static unsigned long lastTrigger;
  if (millis() - lastTrigger >= 1000) {
    lastTrigger = millis();

    // Read both averaged voltages
    payload.batteryVoltage = batteryAverage();
    payload.vcc = vccAverage();

    if (battSense) {  // Observe battery voltage
      if (payload.batteryVoltage <= cutoffVoltage) payload.batteryOk = false;
    } else {  // Observe vcc voltage
      if (payload.vcc <= cutoffVoltage) payload.batteryOk = false;
    }
  }
}

// Voltage read & averaging subfunctions -----------------------------------------
// vcc ----
float vccAverage() {
  static int raw[6];

  if (raw[0] == 0) {
    for (int i = 0; i <= 5; i++) {
      raw[i] = readVcc();  // Init array
    }
  }

  raw[5] = raw[4];
  raw[4] = raw[3];
  raw[3] = raw[2];
  raw[2] = raw[1];
  raw[1] = raw[0];
  raw[0] = readVcc();
  float average = (raw[0] + raw[1] + raw[2] + raw[3] + raw[4] + raw[5]) / 6000.0;
  return average;
}

// battery ----
float batteryAverage() {
  static int raw[6];

  if (!battSense) return 0;

  if (raw[0] == 0) {
    for (int i = 0; i <= 5; i++) {
      raw[i] = analogRead(BATTERY_DETECT_PIN);  // Init array
    }
  }

  raw[5] = raw[4];
  raw[4] = raw[3];
  raw[3] = raw[2];
  raw[2] = raw[1];
  raw[1] = raw[0];
  if (isDriving && HP) raw[0] = (analogRead(BATTERY_DETECT_PIN) + 31);              // add 0.3V while driving (HP version only): 1023 steps * 0.3V / 9.9V = 31
  else raw[0] = analogRead(BATTERY_DETECT_PIN);                                     // else take the real voltage (compensates voltage drop while driving)
  float average = (raw[0] + raw[1] + raw[2] + raw[3] + raw[4] + raw[5]) / 619.999;  // 1023steps / 9.9V * 6 = 619.999
  return average;
}

//
// =======================================================================================================
// MAIN LOOP
// =======================================================================================================
//

void loop() {

  // Read radio data from transmitter
  readRadio();

  // Exponential throttle and steering
  exponentialCurves();

  // Write the servo positions
  writeServos();

  // ESC speed signals with steering overlay
  driveMotorsSteering();

  // Internal TB6612-FNG motor driver
  driveMotors();

  // Battery check
  checkBattery();

  // Digital Outputs (special functions)
  digitalOutputs();
}

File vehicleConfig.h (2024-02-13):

#ifndef vehicleConfig_h
#define vehicleConfig_h

#include "Arduino.h"

#define CONFIG_OPEN_RC_TRACTOR // <- Select the correct vehicle configuration here before uploading! CONFIG_WPL_B_36_MODE1  CONFIG_CATERPILLAR_TEST  CONFIG_KING_HAULER

// NOTE: SBUS not usable if "TXO_momentary1" or "TXO_toggle1" or "headLights" or DEBUG!
#define SBUS_SERIAL // serial connection uses SBUS protocol instead of normal protocol, if not commented out

#define ESC_MICROSECONDS // ESC controlled in microseconds instead of degrees (experimental)

//
// =======================================================================================================
// VEHICLE SPECIFIC CONFIGURATIONS
// =======================================================================================================
//

/*
  // Battery type
  boolean liPo; // If "true", the vehicle can't be reactivated once the cutoff voltage is reached
  float cutoffVoltage; // Min. battery discharge voltage, or min. VCC, if board rev. < 1.2 (3.6V for LiPo, 1.1 per NiMh cell)

  // Board type (see: https://www.youtube.com/watch?v=-vbmHhCvspg&t=18s)
  float boardVersion; // Board revision (MUST MATCH WITH YOUR BOARD REVISION!!)
  boolean HP; // HP = "High Power" version (both TB6612FNG channels wired in parallel) -> No motor 1, motor 2 is the driving motor

  // Vehicle address
  int vehicleNumber; // This number must be unique for each vehicle!

  // Vehicle type
  byte vehicleType;
  0 = car (see: https://www.youtube.com/watch?v=A0SoK7KJxyc). Use this mode, if you want to use indicators. No MPU-6050 MRSC support.
  1 = semi caterpillar, 2 = caterpillar (see: https://www.youtube.com/watch?v=Tjikm6hJ8hQ)
  3 = forklift (see: https://www.youtube.com/watch?v=3iXL9WvE4ro)
  #define VEHICLE_TYPE_3_WITH_ESC = forklift or dumper with separate ESC, motor driver 1 is controlled by CH 4
  4 = balancing (see: https://www.youtube.com/watch?v=zse9-l2Yo3Y)
  5 = car with MRSC (Micro RC Stability Control). Similar with ABS, ESP, Traxxas Stability Management TSM. Potentiometer on A6 input of
  your transmitter required! (see: https://www.youtube.com/watch?v=IPve7QpdLBc&t=5s) Indicators can't be used in this mode (locked)!
  6 = simple dual motor plane with differential thrust steering. No rudders.

  // MRSC
  #define MRSC_FIXED // Only use this definition, if you want to use an MRSC vehicle without a gain adjustment pot on your transmitter
  byte mrscGain = 25; // 25%

  // Lights (see: https://www.youtube.com/watch?v=qbhPqHdBz3o , https://www.youtube.com/watch?v=wBTfsIk4vkU&t=84s)
  boolean tailLights; // Caution: the taillights are wired to the servo pin 2! -> Servo 2 not usable, if "true"
  boolean headLights; // Caution: the headlights are wired to the RXI pin! -> Serial not usable, if "true"
  boolean indicators; // Caution: the indicators are wired to the SDA / SCL pins! -> not usable, if vehicleType is 4 or 5 (locked)
  boolean beacons; // Caution: the beacons are wired to the servo pin 4! -> Servo 4 not usable, if "true"

  // Servo limits (45 - 135 means - 45° to 45° from the servo middle position)
  #define STEERING_3_POINT_CAL // steering center point is separately adjustable
  byte lim1L, lim1C, lim1R; // Servo 1, Lim1C for STEERING_3_POINT_CAL option (center position)
  byte lim2L, lim2C, lim2R; // Lim2C for THREE_SPEED_GEARBOX option (center position)
  byte lim3L, lim3R;
  byte lim3Llow = 75, lim3Rlow = 105; // limited top speed angles for external ESC
  byte lim4L, lim4R; // Servo 4, also used for tractor trailer unlocking servo (TRACTOR_TRAILER_UNLOCK option)
  #define TWO_SPEED_GEARBOX // Vehicle has a mechanical 2 speed shifting gearbox, switched by servo CH2. Not usable in combination with the "tailLights" option
  #define THREE_SPEED_GEARBOX // Vehicle has a mechanical 3 speed shifting gearbox, switched by servo CH2. Not usable in combination with the "tailLights" option

  // Motor configuration
  int maxPWMfull; // (100% PWM is 255)
  int maxPWMlimited;
  int minPWM; // backlash compensation for self balancing applications
  byte maxAccelerationFull;// (ms per 1 step input signal change)
  byte maxAccelerationLimited;

  // Variables for self balancing (vehicleType = 4) only!
  float tiltCalibration = -0.2; // -0.2° (+ = leans more backwards!) Vary a bit, if you have slow oscillation with big amplitude

  // Steering configuration (100% torque is 255)
  byte steeringTorque;

  // Motor 2 PWM frequency: 32 = 984Hz (default), 8 = 3936Hz, 1 = 31488Hz (only with board version. 1.3 or newer)
  byte pwmPrescaler2; // Motor 2 = steering motor (or driving motor in "HP" High Power board version)

  // Additional Channels
  boolean TXO_momentary1; // The TXO output is linked to the momentary1 channel! -> Serial not usable, if "true"
  boolean TXO_toggle1; // The TXO output is linked to the toggle1 channel! -> Serial not usable, if "true"
  boolean potentiometer1; // The potentiometer knob on the transmitter is linked to the servo output CH4
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

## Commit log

2016-08-09 Board optimized
    [Micro RC Receiver.brd, Micro RC Receiver.sch]
2016-09-13 Variant for Dodge Challenger with taillights & brake lights
2016-10-09 V1.5 with caterpillar steering mixer
2016-11-05 V1.61: battery cutoff bug fixed
    [Micro_RC_Receiver.ino]
2016-11-29 V1.7: support for board V1.3 and "High Power" board variant
2016-11-30 V 1.3 HP (High Power)
    [Micro RC Receiver HP.brd, Micro RC Receiver HP.sch]
2016-11-30 V 1.3
    [Micro RC Receiver.brd, Micro RC Receiver.sch]
2016-12-11 V1.71: battery cutoff triggering improved
2017-02-23 V1.4
    GND plane and decoupling improved
    [Micro RC Receiver.brd, Micro RC Receiver.sch]
2017-08-08 Bill of Material added
2017-10-08 V2.3: MRSC (Micro RC Stability Control) ESC added
    MPU-6050 required
    [Micro_RC_Receiver.ino, vehicleConfig.h]
2017-10-29 V2.32: Flickering headlights bug in vehicleType 5 fixed
    [Micro_RC_Receiver.ino, vehicleConfig.h]
2017-12-05 MPU-6050 shield Eagle PCB added
2017-12-08 V2.5: MRSC now also working with DC steering motor
2018-02-04 Receiver Labels added
    [Label.xlsx]
2018-02-04 STL housing data for 3D printing added
    [Bottom Housing.stl, Top Housing Dual DC Motors.stl, Top Housing High Power.stl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]
2018-02-04 STL data for 3D printing added
    [Pin Header Cover 2x.stl, Pin Header Cover 3x.stl, Pin Header Cover 4x.stl]
2018-02-11 BOM typo fixed
2018-04-10 V2.7: Gain adjustment pot can be linked to servo CH4
2018-08-26 V2.8: support for differential thrust controlled planes
2018-11-06 V2.9: support for mechanical 2 speed gearbox control
2019-09-24 V3.1: Added THRE_SPEED_GEARBOX option
    For 3 speed transmissions, controlled by a 3 position switch
2019-12-27 v3.3: serial communication for ESP32 engine sound added
2020-01-04 v3.32: minor bug fixed
    [Micro_RC_Receiver.ino]
2020-04-10 V1.5: board slightly optimised, Gerbers included
    [Micro RC Receiver.brd, Micro RC Receiver.sch]
2020-05-23 Housings with clips added
    [Receiver Top Clip Dual Motors.stl, Receiver Top Clip No Motor.stl, Receiver Top Clip Single Motor.stl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]
2020-05-24 current pictures added
2020-11-01 v3.6: dual ESC steering mixer added (see changelog)
2020-12-21 V3.7: Steering center position separately adjustable
2021-04-02 Nano SBUS board added
    [BOM.xlsx, Micro RC Receiver.brd, Micro RC Receiver.sch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]
2024-02-13 forklift version added
    [forklift steering angle.xlsx]

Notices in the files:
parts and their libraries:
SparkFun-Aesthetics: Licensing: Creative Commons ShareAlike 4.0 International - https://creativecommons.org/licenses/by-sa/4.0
